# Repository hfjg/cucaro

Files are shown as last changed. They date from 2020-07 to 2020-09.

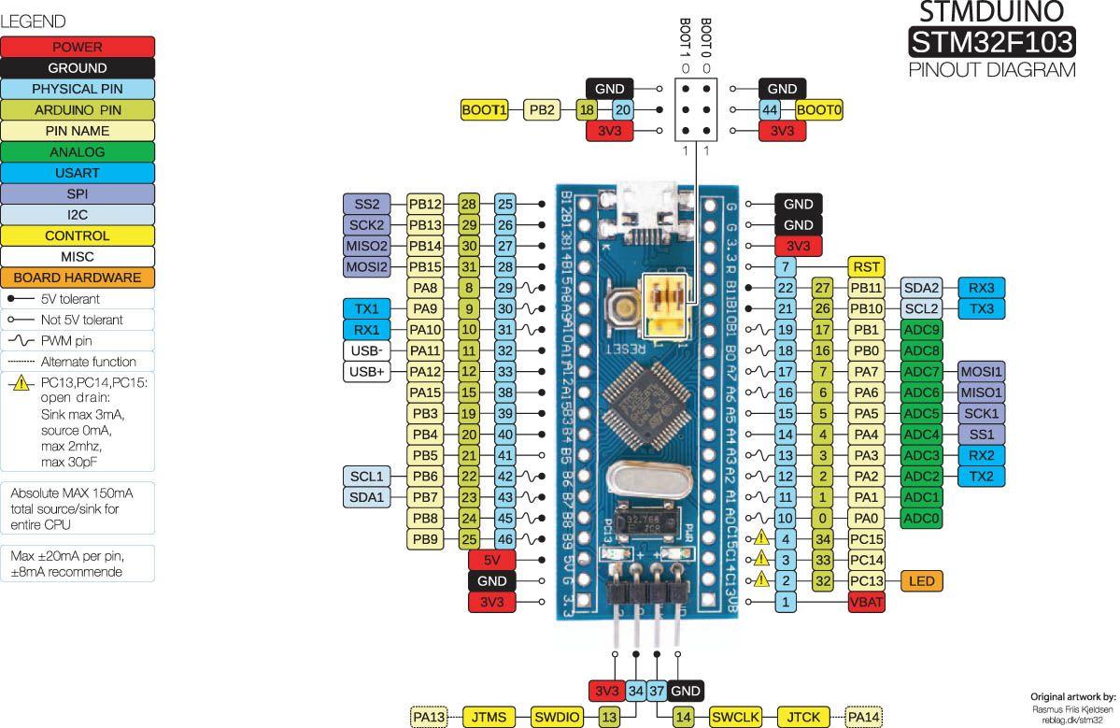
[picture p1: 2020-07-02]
Modules/02_BatMan/Firmware/doc/STM32_Pinout.jpg

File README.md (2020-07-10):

CuCaRo is a **Cu**riosity Inspired **Ca**mera **Ro**ver, roughly adopting the shape, chassis and drive/steer mechanisms.

# Overview
CuCaRo is built of following modules:
(For more details please refer to the module documentation).
1. [Body](./Modules/01_Body/Documents/01_Body_README.md)
2. [BatMan](./Modules/02_BatMan/Documents/02_BatMan_README.md) (The Battery Manager)
3. DriSu (Drive and STeering units, six in total)
3. ACOS (Anti Collision Sensors)
4. RunCam

Modules communicate with each other via CAN-Bus.

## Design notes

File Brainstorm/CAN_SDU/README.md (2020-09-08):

# CAN-SDU
Steer and Drive Unit with CAN-Bus

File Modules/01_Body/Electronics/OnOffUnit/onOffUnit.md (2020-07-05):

#On-Off-Unit
The on-off-unit ensures that the Raspberry Pi is switched off correctly, i.e. it can do ist shutdown process.

## Specification
* One button operation 
    * If off, button press turns on SBC Power Supply
    * If on, short button press initiates reset, long press initiates shutdown

* Additional functions
    * Battery Charge Control
    * Buffered internal battery to initiate shutdown on battery fail during operation
    * Measurement of 
        * Battery voltage
        * Battery Current
        * Charger voltage 
      and option to readout values via I2C.

## Realisation
Microcontroller communicates with SBC via I2C.

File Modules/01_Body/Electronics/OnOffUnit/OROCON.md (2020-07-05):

# OROCON: On-Reset-Off-Controller
OROCON ensures that the Single-Board_Computer (i.e. Raspberry Pi) is shut down correctly.  Communication to SBC is via I2C.

## Specification
* One button operation 
    * If off, button press turns on SBC Power Supply
    * If on, short button press initiates reset, long press initiates shutdown

* Additional functions
    * SLA Battery Charge Control
    * Buffered internal battery to initiate shutdown on battery fail during operation
    * Measurement of 
        * Battery voltage
        * Battery Current
        * Charger voltage 
      and option to readout values via I2C.

## Connectors
* Battery in (XT60)
* Charger in (DC Barrel Jack)

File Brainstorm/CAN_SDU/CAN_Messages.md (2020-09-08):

# Steer Messages
* SetAngleDegrees nn

# Drive Messages

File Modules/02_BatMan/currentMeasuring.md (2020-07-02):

# BatMan Memos

## Current measurement
Sensor will be ACS-712 analog sensor.

Output: U_{ACS}=2500mV + k * I

where 
* k=185mV/A for ACS712-5,
* k=100mV/A for ACS712-20 and 
* k=66mV/A for ACS712-30

For the ADC values this yields:
n_{ADC} = (2^N-1) * U_{ADC}/U_{Ref}

and for the (reverse) sensitivity:
dI/dn = U_{Ref} / (k * (2^N-1) )

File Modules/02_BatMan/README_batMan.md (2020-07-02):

# BatMan
Battery management module for CuCaRo

## Components
* Arduino Pro Mini
* CAN-Interface with MCP2515
* 16-Bit ADC-Module ADS1115
* Current Sensor ACS712
* Temperature Sensor (type tbd)
* 2x LM2596, one for VECU (5V), one for charger

## Firmware functions
- Module attaches as I2C-Slave or as CAN-Module (tbd)
- Periodically measure voltages (10/s),  current (10/s), batteryTemperature (1/s)
- Check for charger, charge if necessary (battery type and data in setup)

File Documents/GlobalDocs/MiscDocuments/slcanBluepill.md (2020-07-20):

#Bluepill as SLCAN adapter

| BluePill | USB-Serial-Adapter | CAN-Transceiver |
|---|---|
| A9 | TX | |
| A10  | RX | |
| A11  | | CRX |
| A12  | TX | CTX |
| 5V | | CAN5V|
| 3V3  | | |
| GND  | GND | GND |

[Firmware here](https://github.com/olliw42/uavcan4hobbyists/blob/master/firmware%20binaries/uc4h-slcan-v009.hex)
Bild:

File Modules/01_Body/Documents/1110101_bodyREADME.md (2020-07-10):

# CuCaRo Body
Since CuCaRo is focused on function (and not on design or appearance of the original), its body is made of a [commercial storage box](https://www.eurobox.de/produktkatalog-eb/stapelbehaelter-geschlossen-400x300x235-mm.html) that holds all the components.

## Components
1. Raspberry Pi as main controller
1. Battery and [BatMan](https://github.com/hfjg/cucaro/blob/master/Modules/02_BatMan/Documents/02_BatMan_README.md)
1. Axis bearings and differential

## Mechanics

## Electronics

## Software
The "main" software on the Raspberry Pi is a collection of [node-red](https://nodered.org/) flows, both for device control and for the user interface.

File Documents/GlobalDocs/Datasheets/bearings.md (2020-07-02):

# Frequently used bearings

[TOC]

## Radial Bearings

### Inner Diameter 6mm
| Name | Inner Diameter/mm | Outer Diameter/mm | Height/mm |
|---|---|---|---|
| MR106 | 6  | 10 | 3 |
| MR126 | 6  | 12 | 4 |
| 686 | 6  | 13 | 5 |
| 626 | 6  | 16 | 6 |

## Axial Bearings
| Name | Inner Diameter/mm | Outer Diameter/mm | Height/mm |
|---|---|---|---|
| F3-8M | 3 | 8,5 | 3,5|
| F6-14M | 6 | 14 | 5|
| F8-16M | 8 | 16 | 5|
| F8-19M | 8 | 19 | 7|
| 51101 | 12 | 26 | 9 |
| 51104 | 20 | 35 | 10 |

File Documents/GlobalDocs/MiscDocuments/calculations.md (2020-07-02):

# Torque Calculations

### Assumptions:
* m = 6 kg
* a = 1 m/s^2
* Wheel diameter 10 cm

### Needed force
F = m a = 6 kg * 1 m/s^2 = 6 N
per wheel
F_w = F/6 = 1 N

### Torque
M = r F = 5 cm * 1 N = 5 Ncm = 50 mN m

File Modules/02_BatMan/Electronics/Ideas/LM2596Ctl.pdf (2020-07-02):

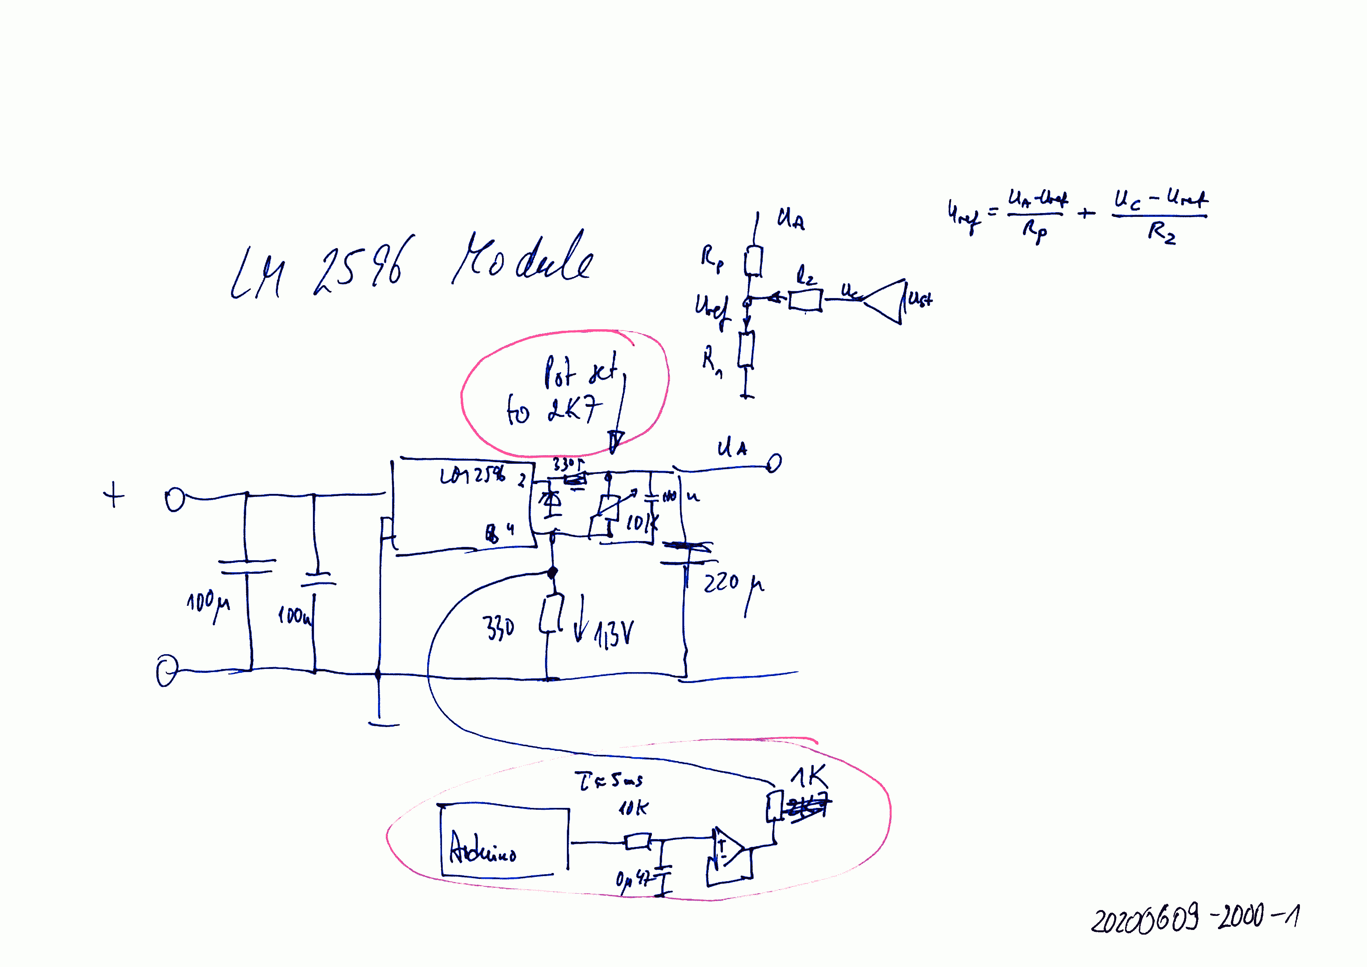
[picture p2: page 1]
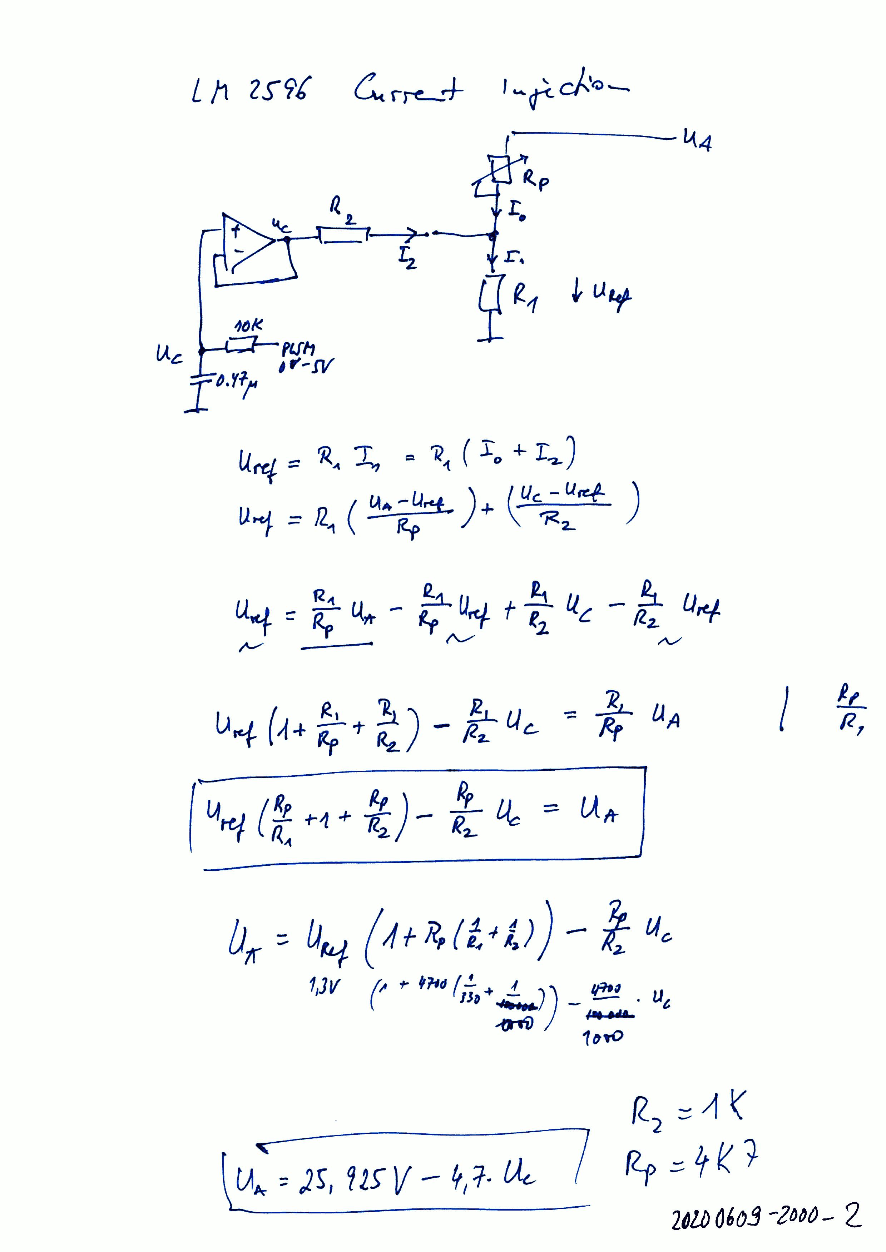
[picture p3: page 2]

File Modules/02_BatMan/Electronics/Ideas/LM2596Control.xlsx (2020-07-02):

U_ref/V | 1.3
R1/Ohm | 330 |  | 1/R1+1/R2
R2/Ohm | 1000 |  | 0.00403030303
 | UC/V
RP/Ohm | 0 | 1 | 2 | 3 | 4 | 5
0 | 1.300 | 1.300 | 1.300 | 1.300 | 1.300 | 1.300
1000 | 6.539 | 5.539 | 4.539 | 3.539 | 2.539 | 1.539
2000 | 11.779 | 9.779 | 7.779 | 5.779 | 3.779 | 1.779
3000 | 17.018 | 14.018 | 11.018 | 8.018 | 5.018 | 2.018
4000 | 22.258 | 18.258 | 14.258 | 10.258 | 6.258 | 2.258
5000 | 27.497 | 22.497 | 17.497 | 12.497 | 7.497 | 2.497
6000 | 32.736 | 26.736 | 20.736 | 14.736 | 8.736 | 2.736
7000 | 37.976 | 30.976 | 23.976 | 16.976 | 9.976 | 2.976
8000 | 43.215 | 35.215 | 27.215 | 19.215 | 11.215 | 3.215
9000 | 48.455 | 39.455 | 30.455 | 21.455 | 12.455 | 3.455
10000 | 53.694 | 43.694 | 33.694 | 23.694 | 13.694 | 3.694
2700 | 15.446 | 12.746 | 10.046 | 7.346 | 4.646 | 1.946
RP/Ohm | 2700
UC/V | UA/V
0 | 15.446
0.2 | 14.906
0.4 | 14.366
0.6 | 13.826
0.8 | 13.286
1 | 12.746
1.2 | 12.206
1.4 | 11.666
1.6 | 11.126
1.8 | 10.586
2 | 10.046
2.2 | 9.506
2.4 | 8.966
2.6 | 8.426
2.8 | 7.886
3 | 7.346
3.2 | 6.806
3.4 | 6.266
3.6 | 5.726
3.8 | 5.186
4 | 4.646
4.2 | 4.106
4.4 | 3.566
4.6 | 3.026
4.8 | 2.486
5 | 1.946

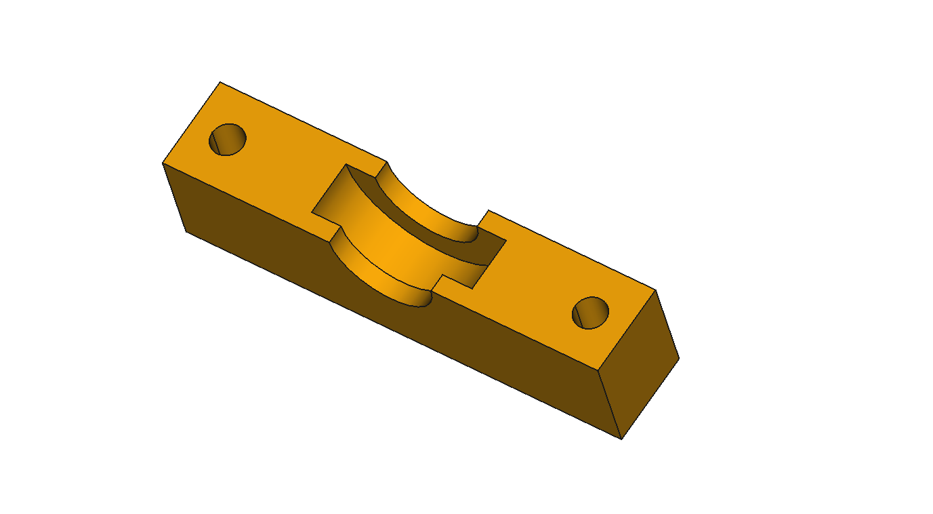
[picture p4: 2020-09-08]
Modules/01_Body/Mechanics/Axis/AxisCarrier/lagerschale_608.png

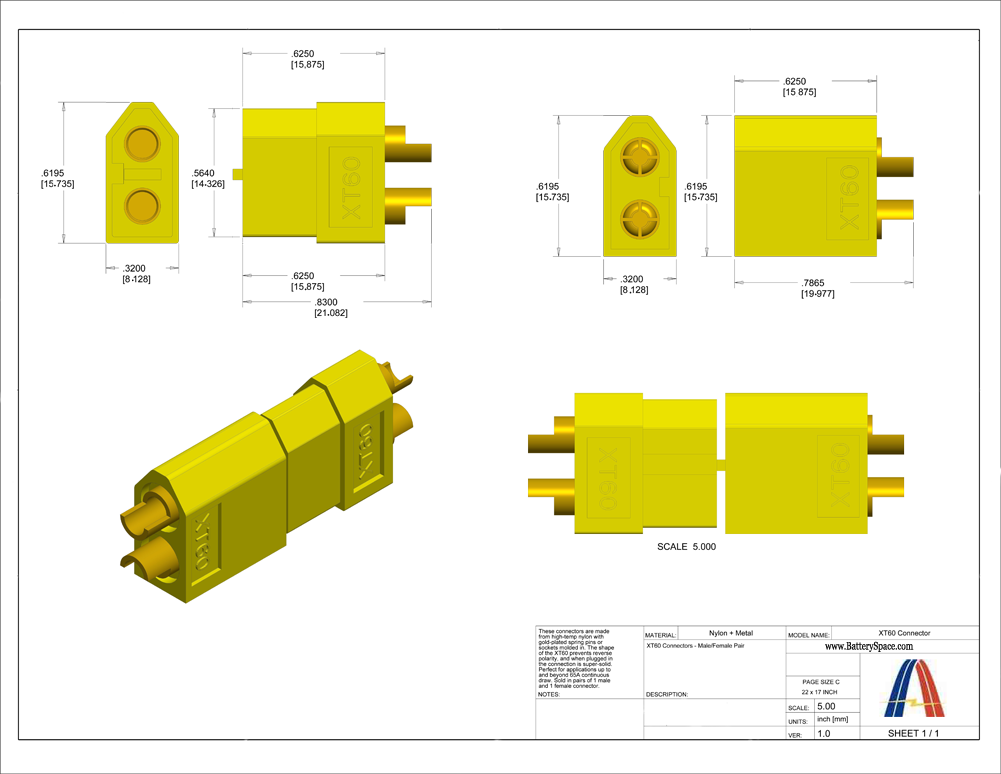
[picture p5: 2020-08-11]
Modules/02_BatMan/Documents/xt60Drawing.png

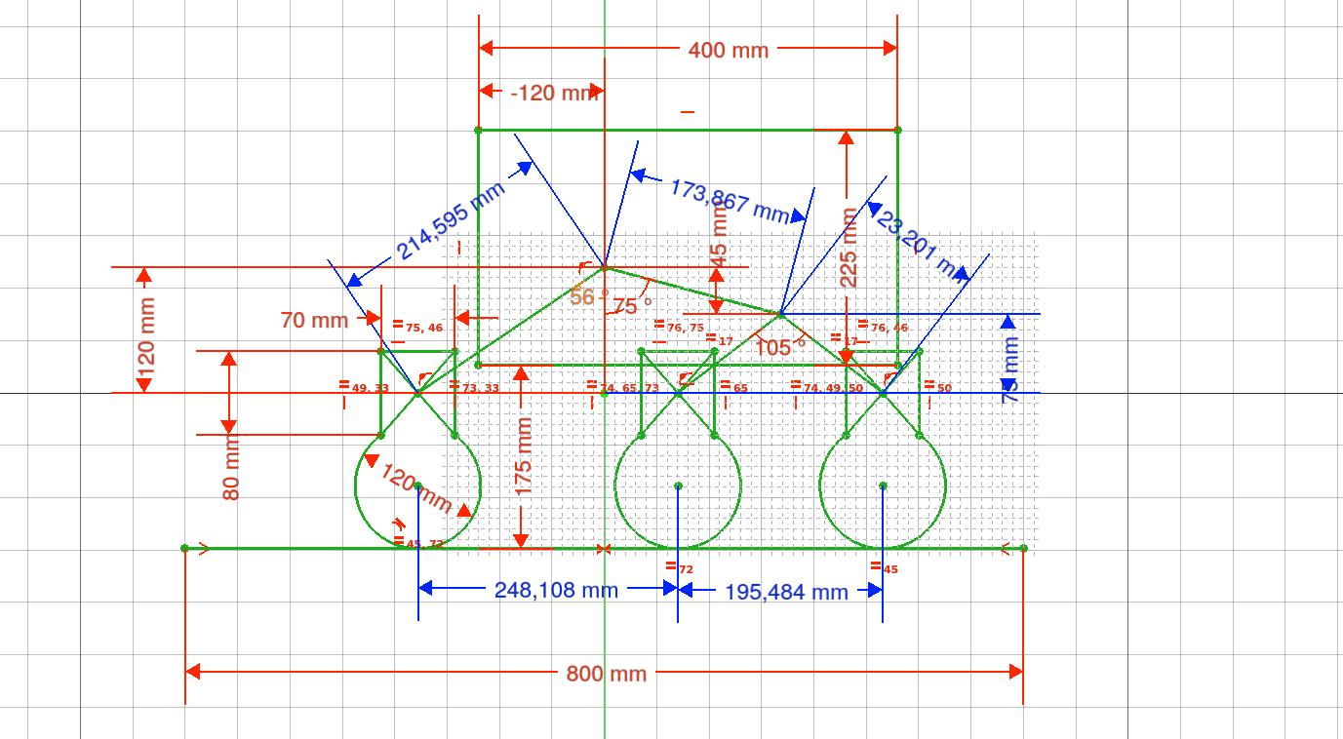
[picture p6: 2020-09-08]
Modules/01_Body/fahrwerk.png

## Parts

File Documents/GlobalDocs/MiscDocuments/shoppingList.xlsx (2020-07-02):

CuCaRo: | Shopping List
Item No. | Desc. | Quantity | Shop | OrderID | exp. Price
1 | TJA1050 | 5 | ebay | 264564374511 | 6.00 €
2 | STM32F103C8T6 | 2 | ebay | 163195692168 | 9.00 €
3 | Servo MG996R | 4+2 | ebay | 254200429981 | 25.00 €
4 | Tires (?) | 4+2 | ebay | 313016459440 | 30.00 €
5 | Pi4-Fan | 1 | berrybase |  | 12.00 €
6 | MPX-Connector | 1x10 | ebay | 221066344116 | 7.95 €
7 | LED-strip | 1 | ebay | 283415013107 | 10.00 €
8 | DC-Dc-Converter, U-I-Limiter | 2 | ebay | 372531513836 | 6.00 €
9 | Dremel Grinder Set |  |  |  | 15.00 €
10
11

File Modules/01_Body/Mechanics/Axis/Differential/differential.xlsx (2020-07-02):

CompNo. | Name | Quantity | Supplier | ItemName
102001 | Body Lower shell | 1 | HG-Printed
102002 | Body Upper shell | 1 | HG-Printed
102003 | Body Fixing Screw | 4 | TBD | M4x20 Allen Head
102004 | Body Fixing Nut | 4 | TBD | M4
102011 | Internal shaft 8 dia x ??? | 1 | TBD
102012 | Internal bevel Gear | 2 | HG-Printed
102013 | Internal Bearing | 2 | GAP | 608
102014 | Internal spacer 8x12x?? | 2 | HG-Printed
102015 | Internal Gear Spacer (optional) | 1 | HG-Printed
102021 | Halfshaft | 2 | TBD | M8x50 Hex Head
102022 | Halfshaft Bearing | 2 | GAP | 608
102023 | Halfshaft spacer 8 x ?? x ?? | 2 | HG-Printed
102024 | Halfshaft bevel Gear | 2 | HG-Printed
102025 | Spacer M8 | 2 | TBD | M8 spacer
102026 | Locknut M8 | 2 | TBD | M8 Locknut

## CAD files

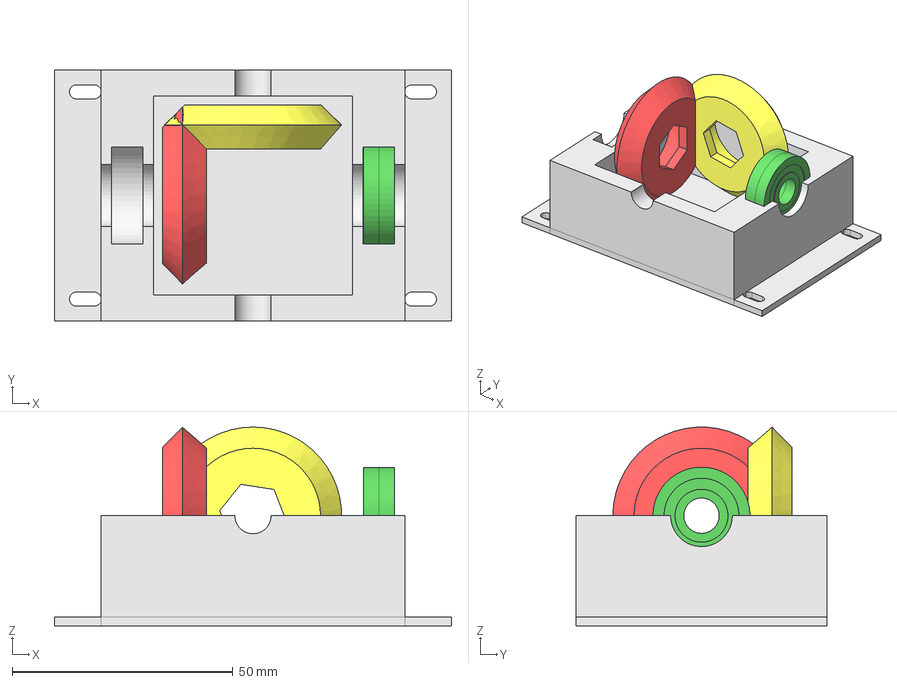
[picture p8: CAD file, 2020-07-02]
Modules/01_Body/Mechanics/Axis/Differential/DiffAssy.FCStd
90.0 x 57.0 x 45.1 mm
cucaroDiff_Box_001
cucaroDiff_608Dummy_001
cucaroDiff_GearwheelDummy_001
cucaroDiff_GearwheelDummy_002

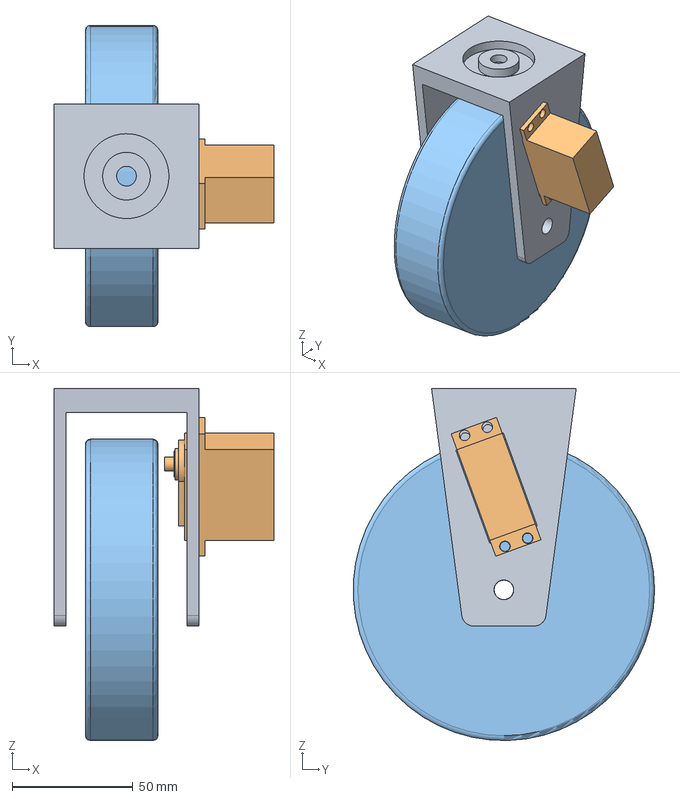
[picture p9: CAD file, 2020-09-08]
Modules/01_Body/Mechanics/Axis/forkHolderAssy.FCStd
91.1 x 124.9 x 146.0 mm
radhalterPollin_001
MG996Dummy_001
radhalterPollin_002

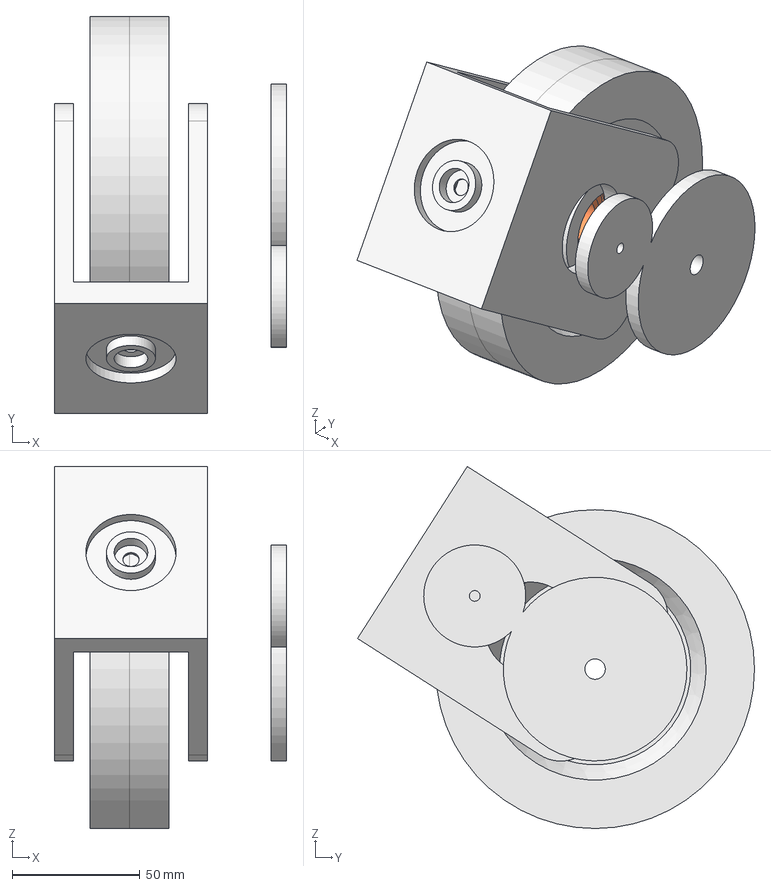
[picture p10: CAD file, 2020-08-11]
Modules/01_Body/Mechanics/Axis/Wheels/pollinWheels/wheelAssy.FCStd
91.0 x 155.7 x 141.9 mm
wheel125_001
bearing6002_001
fork_001
gearWheelDummy_001

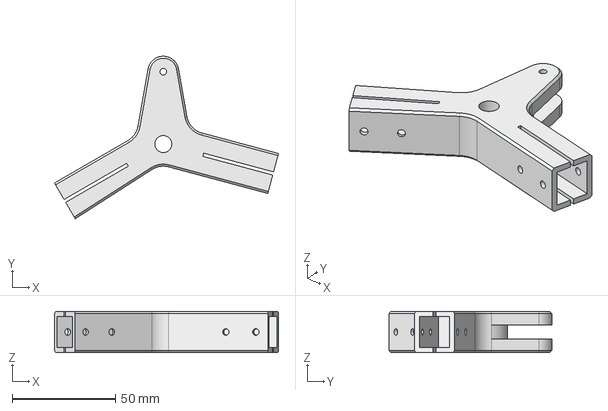
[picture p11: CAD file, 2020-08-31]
axisHolderFront.FCStd
108.3 x 78.7 x 20.0 mm

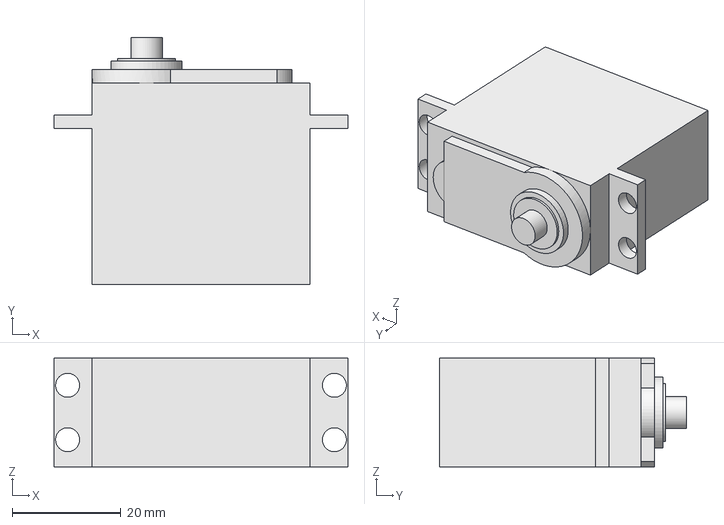
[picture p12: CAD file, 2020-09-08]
Documents/Datasheets/MG996Dummy.FCStd
54.0 x 45.3 x 20.0 mm

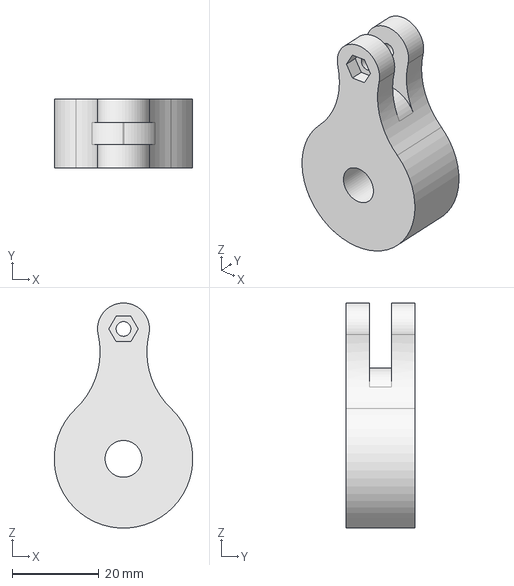
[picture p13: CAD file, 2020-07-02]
Modules/01_Body/Mechanics/Axis/AxisCarrier/EarlierDesigns/schwinge.FCStd
32.0 x 16.0 x 52.0 mm

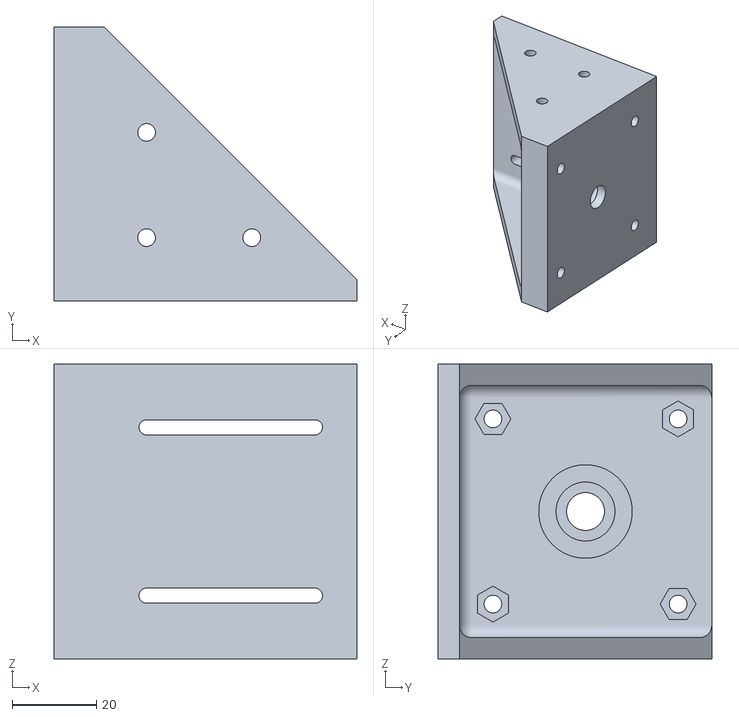
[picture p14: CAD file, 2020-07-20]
Modules/01_Body/Mechanics/Axis/AxisCarrier/STL/axisHolderInner_R03.stl
72.0 x 65.0 x 70.0

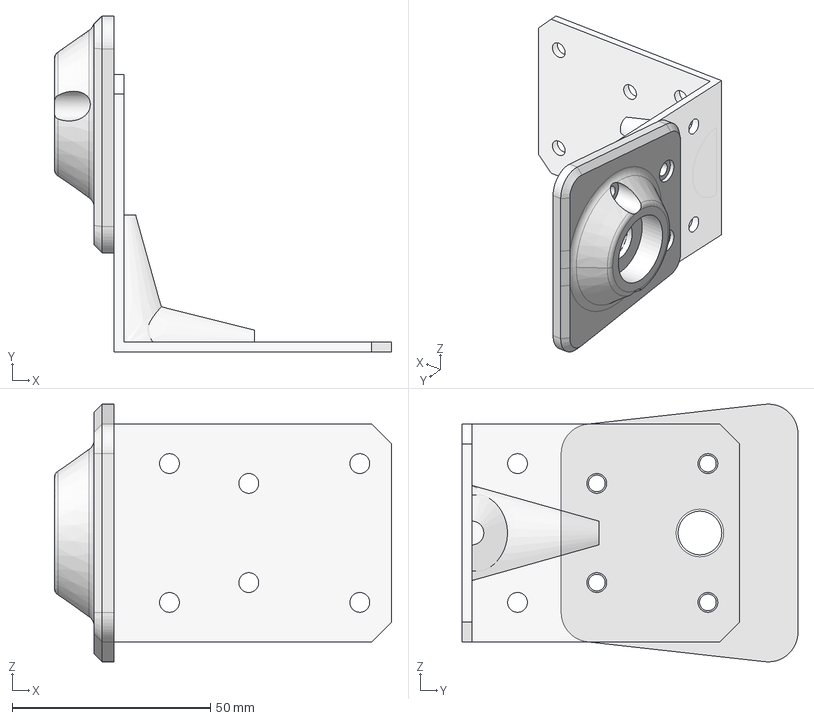
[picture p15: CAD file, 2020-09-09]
Modules/01_Body/Mechanics/Axis/CUAB_CustomAngleBracket.FCStd
85.0 x 84.7 x 65.0 mm
bearingHolderOutside

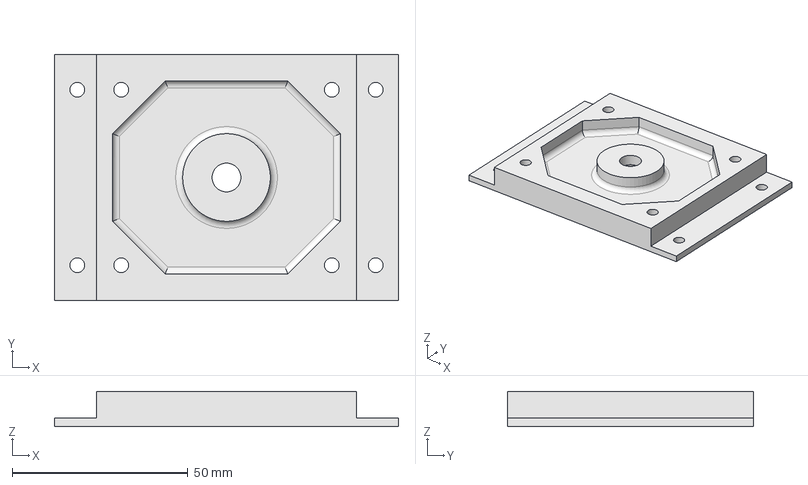
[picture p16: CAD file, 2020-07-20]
Modules/01_Body/Mechanics/Axis/Differential/baseplate.FCStd
98.0 x 70.0 x 10.0 mm

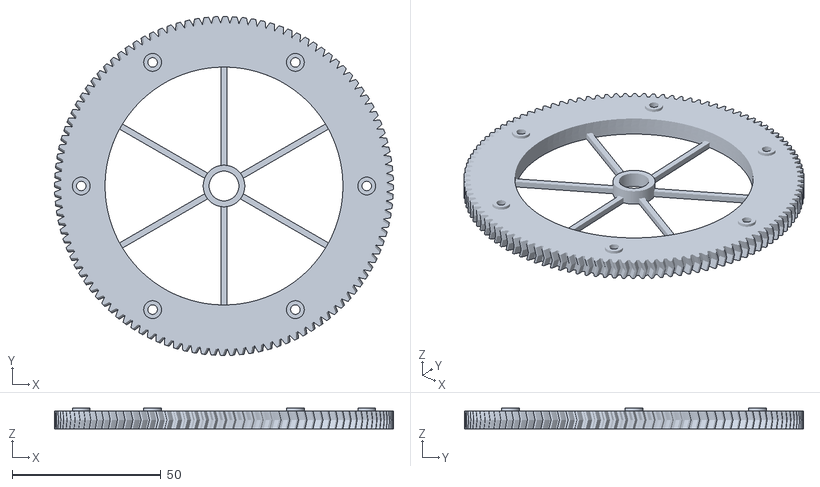
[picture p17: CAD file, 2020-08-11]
Modules/01_Body/Mechanics/Axis/Wheels/pollinWheels/driveGearWheel_02A.stl
114.0 x 114.0 x 6.95

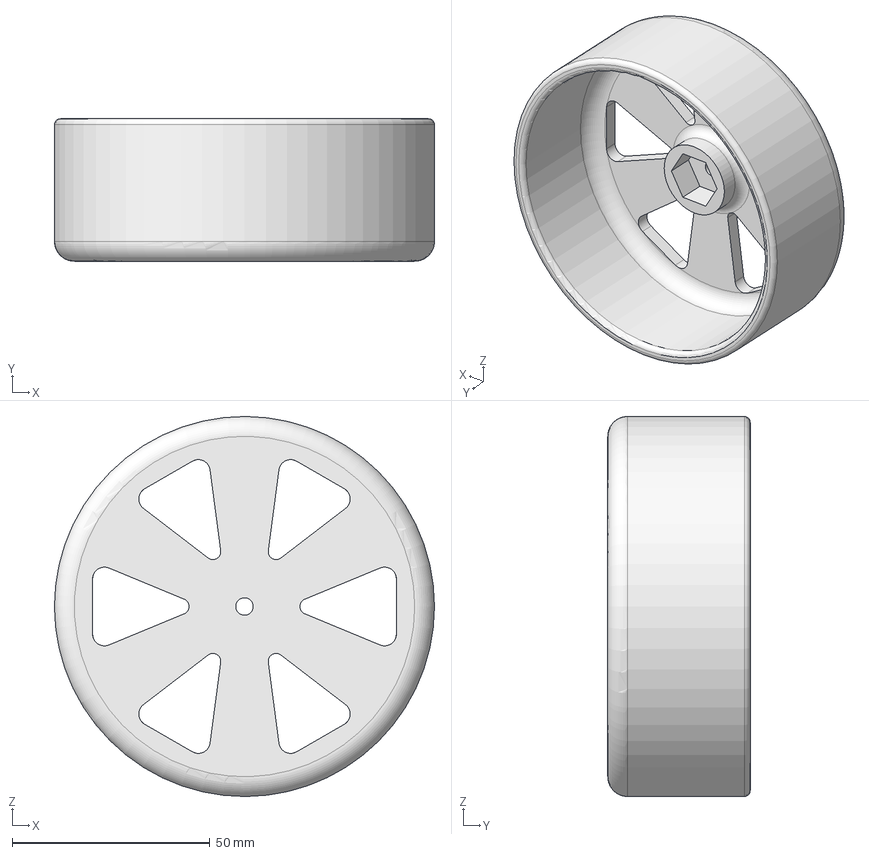
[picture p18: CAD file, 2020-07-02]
Modules/01_Body/Mechanics/Axis/Wheels/wheel_R02.FCStd
96.0 x 36.0 x 96.0 mm

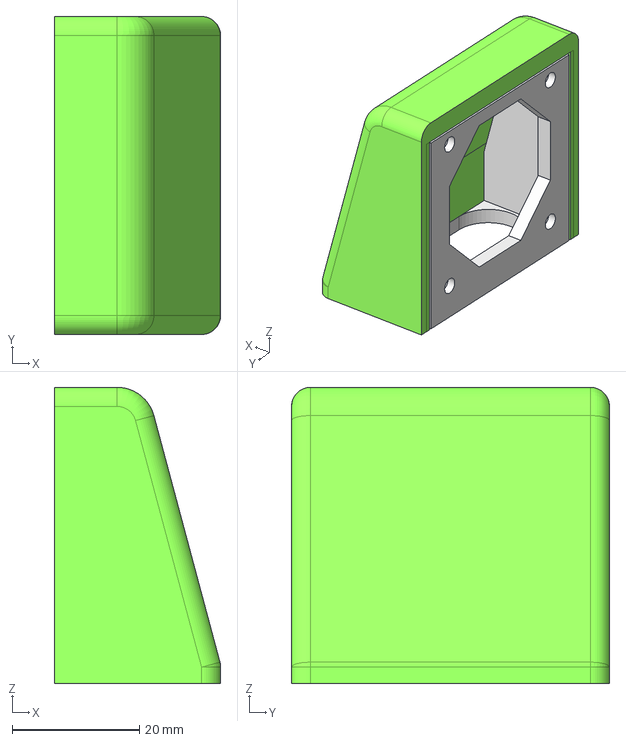
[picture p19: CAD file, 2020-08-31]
Modules/01_Body/Mechanics/Mounts/fanMount_B.FCStd
26.2 x 50.0 x 46.6 mm
wallPlate
cover

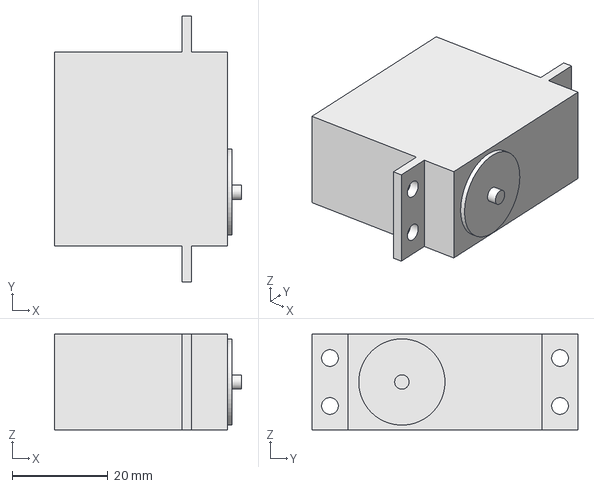
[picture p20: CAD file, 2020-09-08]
Documents/Datasheets/MG995Dummy.FCStd
39.1 x 55.5 x 20.0 mm

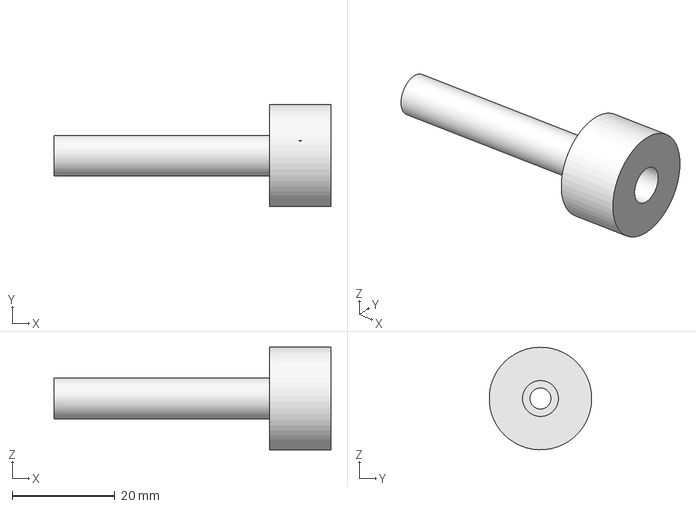
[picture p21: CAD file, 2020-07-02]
Modules/01_Body/Mechanics/Axis/AxisCarrier/EarlierDesigns/radmitnehmerPollin.FCStd
54.0 x 20.0 x 20.0 mm

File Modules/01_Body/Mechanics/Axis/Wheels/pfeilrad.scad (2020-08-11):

use <hg_zahnradlib.scad>
use <baConEl.scad>

zBig = 106;
zSmall = 24;
zModule = 1;
axisDistance = (zBig+zSmall)/2/zModule;
echo("Axis distance = ", axisDistance);

module bigWheel(){
    difference(){
        union(){
            pfeilrad(modul=zModule, zahnzahl=zBig, hoehe=5, bohrung=84, eingriffswinkel = 20, schraegungswinkel = 20);
            tube(do=28.4, wall=2.4, length=6);
            circleOf(num=6, r=28/2, startAngle=30) translate([0,-0.5,0])cube([40,1.4,1.4]);
        }
        
        circleOf(num=6, r=94/2){
            cylinder(d=3.2, h=20, center=true);
            translate([0,0,-0.05])cylinder(d1=5.6, d2=3.2, h=2.2);
           
        }
         circleOf(num=6,r=24)translate([-15,-4,3])cube([8,8,10]);
    }
}

module smallWheel(){
    pfeilrad(modul=zModule, zahnzahl=zSmall, hoehe=4, bohrung=3, eingriffswinkel = 20, schraegungswinkel = -20);
}

bigWheel();

translate([(zBig+zSmall)/2/zModule,0,0.50])rotate([0,0,360/zSmall/2])smallWheel();

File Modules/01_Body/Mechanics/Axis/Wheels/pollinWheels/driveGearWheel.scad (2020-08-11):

use <hg_zahnradlib.scad>
use <baConEl.scad>

module carrier(zz=60, drillDia=8.2, wx=4, pfeil=20){
    difference(){
        union(){
            //pfeilrad(modul=1, zahnzahl=zz, hoehe=6, bohrung=2, eingriffswinkel = 20, schraegungswinkel = pfeil);


  pfeilhohlrad(modul=1, zahnzahl=zz, hoehe=10, randbreite=5, eingriffswinkel = 20, schraegungswinkel = 0);
            
            cylinder(d=40, h=2);
            for (phi=[0:90:179]) rotate([0,0,phi])translate([-(zz-5)/2,-wx/2,-3])
                cube([zz-5,wx,3]);
        }
        cylinder(d=drillDia, h=20, center=true);
    }
}

r = 45;
zh = 6;
z1 = 12;
z2 = z1 + 2*r;

color("green")translate([r,0,0])pfeilrad(modul=1, zahnzahl=z1, hoehe=zh, bohrung=4, eingriffswinkel = 20, schraegungswinkel = -15);

!union(){
    difference(){
        translate([0,0,-2]){
            translate([0,0,-3])tube(di=80, do=114.333, length=3);
            tube(di=105, do=114.333, length=3);
            translate([0,0,-3])tube(di=8.2, do=14, length=3);
            
            circleOf(r=6, num=6, startAngle=30)translate([0,-4,-3])cube([45,8,3]);
        }
        circleOf(r=45, num=6){
           cylinder(d=3.2, h=20, center=true);
           translate([0,0,-3+0.05])cylinder(d2=5.8, d1=3.2);
        }
    }

    pfeilhohlrad(modul=1, zahnzahl=z2, hoehe=zh, randbreite=5, eingriffswinkel = 20, schraegungswinkel = 15);
}

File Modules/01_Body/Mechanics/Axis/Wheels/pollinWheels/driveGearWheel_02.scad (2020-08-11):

use <hg_zahnradlib.scad>
use <baConEl.scad>

zh = 6;
z1 = 48;
z2 = 112;
r = (z1+z2)/2;
screwDia = 3.2;

echo ("r = ", r);
echo ("gear ratio = ", z2/z1);

module antrieb(){
    color("green")translate([r,0,0])pfeilrad(modul=1, zahnzahl=z1, hoehe=zh, bohrung=4.2, eingriffswinkel = 20, schraegungswinkel = -15);
}


module abtrieb(){
   
    difference(){
        union(){
            pfeilrad(modul=1, zahnzahl=z2, hoehe=zh, 
            bohrung=z2-32, eingriffswinkel = 20,
            schraegungswinkel = 15);
        
        // hub
            tube(di=10, wall=2, length=5);
        
        // spokes (break away after monting gearwheel)
            spokeWidth = 2;
            spokeHeight = 2;
            circleOf(r=6, num=6, startAngle=30)
                translate([0,-spokeWidth/2,0])cube([z2/2-10,spokeWidth,spokeHeight]);
            circleOf(r=z2/2-8, num=6)
               translate([0,0,zh-0.05])tube(di=screwDia, do=6, length=1);
        }
        
        // mount holes
        circleOf(r=z2/2-8, num=6){
           cylinder(d=screwDia, h=20, center=true);
           translate([0,0,-0.05])cylinder(d1=5.8, d2=screwDia);
        }
    }

}

wheelWidth = 32;
translate([0,0,-(wheelWidth/2+1+zh)]){
    antrieb();
    !abtrieb();
}
%axis();
%wheel();

module axis(){cylinder(d=8, h=60, center=true);}
module wheel(){tube(do=120, di=8, length=32, center=true);}

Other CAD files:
Modules/01_Body/skizzeFahrwerk.FCStd
Modules/01_Body/Mechanics/Axis/AxisCarrier/STL/flexibleCoupling-8x8x30.stl
Modules/01_Body/Mechanics/Axis/Wheels/pollinWheels/wheel125.FCStd
Modules/01_Body/Mechanics/Mounts/fanMount_A1.FCStd
Modules/01_Body/Mechanics/Axis/AxisCarrier/Flexible_Coupling.scad
Modules/01_Body/Mechanics/Axis/1220403_axisHolderFrontBase.FCStd
Modules/01_Body/Mechanics/Axis/1220403_axisHolderFrontLeftInner.FCStd
Modules/01_Body/Mechanics/Axis/1220403_axisHolderFrontLeftOuter.FCStd
Modules/01_Body/Mechanics/Axis/1220403_axisHolderLeftInner.stl
Modules/01_Body/Mechanics/Axis/1220403_axisHolderLeftOuter.stl
Modules/01_Body/Mechanics/Axis/AxisCarrier/1110101_axisAssy.FCStd
Modules/01_Body/Mechanics/Axis/AxisCarrier/1210101_axisCarrierPlate.FCStd
Modules/01_Body/Mechanics/Axis/AxisCarrier/1220105_axisHolderOuter.FCStd
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

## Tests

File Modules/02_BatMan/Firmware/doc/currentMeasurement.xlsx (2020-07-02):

ACS712 calculations |  |  | V_REF/mV | N | V_REF/mV | N
 |  |  | 5000 | 10 | 3300 | 12
Model | Sensitivity / (mV/A) | Offset / mV | mA per LSB |  | mA per LSB
ACS712-5 | 185 | 2500 | 26.4 |  | 6.6
ACS712-20 | 100 | 2500 | 48.9 |  | 12.2
ACS712-30 | 66 | 2500 | 74.1 |  | 18.5

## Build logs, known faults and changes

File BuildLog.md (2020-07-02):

# Build Log

## 2020-05-01
Finished wheel assembly, printed test parts (hex hub and lower axial bearing holder).

## 2020-04-13
Ported Differential ends to OpenSCAD. To omit heat inserts, redesigned ends as cylinder and hat. Cylinder holds M8 nut for the differential bar, hat holds M3 nut for turnbuckle. The two parts are screwed together with 3 M3 screws.
Printing: Hat should be printed small end down, usung brim if necessary. Cylinder shoulf be printed with M8-nut up. Both parts with no supports!

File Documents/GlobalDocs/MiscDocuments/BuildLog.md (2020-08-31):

# Build Log

## 2020-08-13
Printed front axle joint. Failed due to tangled filament. 
**Idea:** Print in two halves -> needs no supports, easier in case of printing failure.

## 2020-07-05
Added holes to differential's halfshaft bevel gear.

## 2020-05-01
Finished wheel assembly, printed test parts (hex hub and lower axial bearing holder).

## 2020-04-13
Ported Differential ends to OpenSCAD. To omit heat inserts, redesigned ends as cylinder and hat. Cylinder holds M8 nut for the differential bar, hat holds M3 nut for turnbuckle. The two parts are screwed together with 3 M3 screws.
Printing: Hat should be printed small end down, usung brim if necessary. Cylinder shoulf be printed with M8-nut up. Both parts with no supports!

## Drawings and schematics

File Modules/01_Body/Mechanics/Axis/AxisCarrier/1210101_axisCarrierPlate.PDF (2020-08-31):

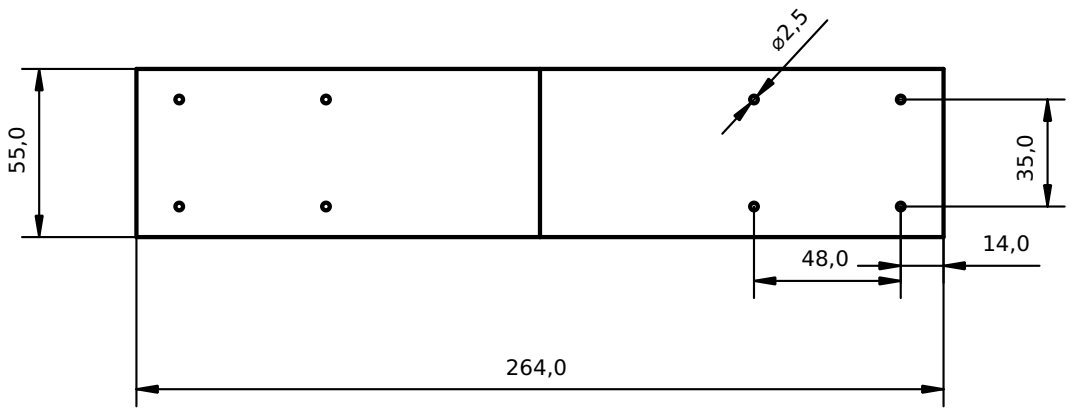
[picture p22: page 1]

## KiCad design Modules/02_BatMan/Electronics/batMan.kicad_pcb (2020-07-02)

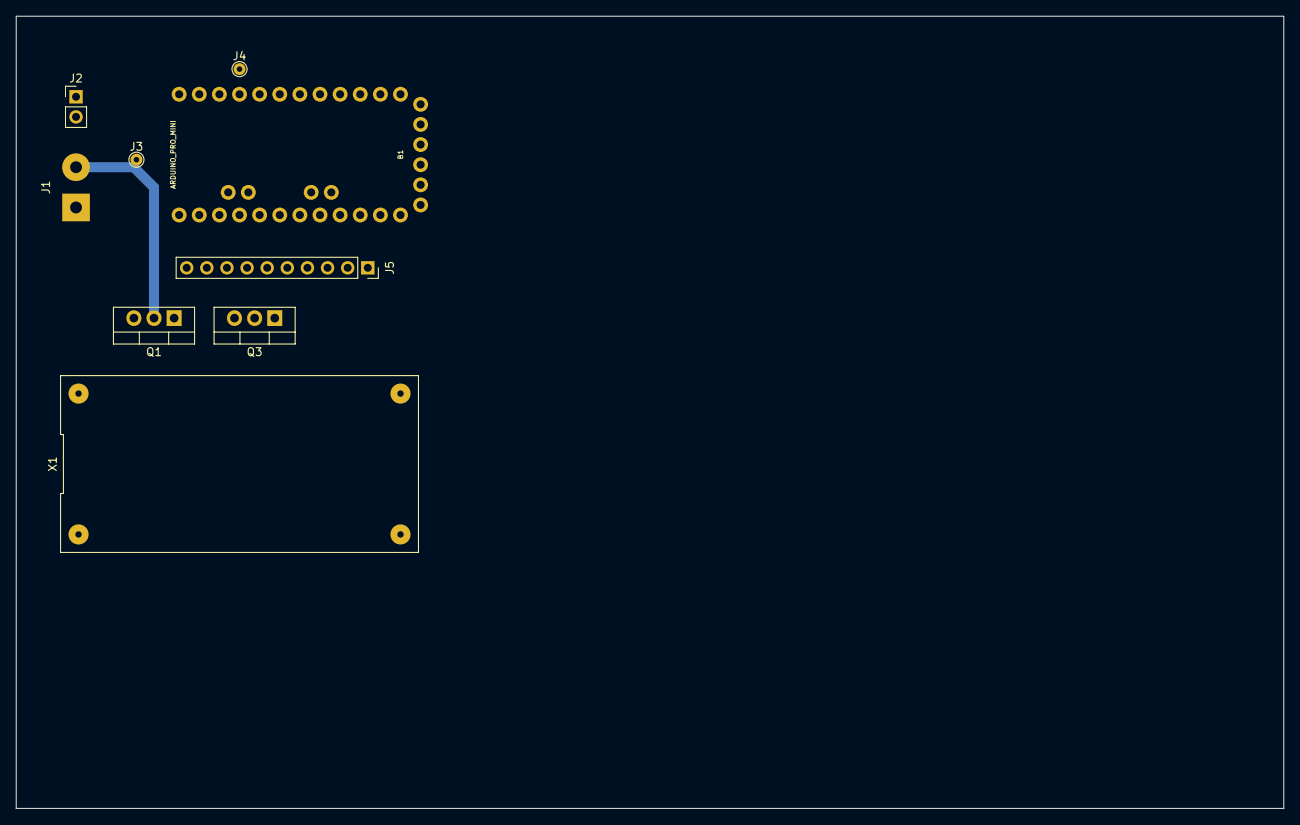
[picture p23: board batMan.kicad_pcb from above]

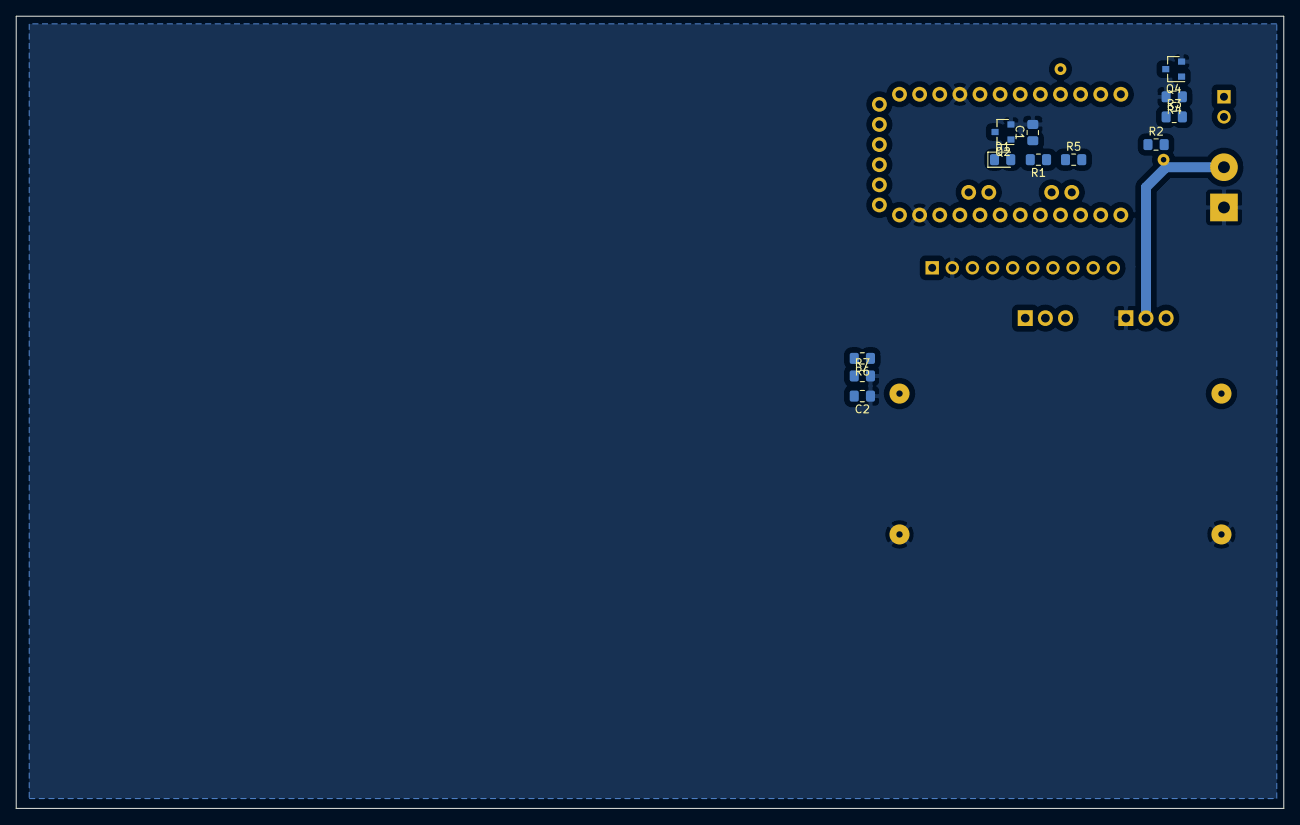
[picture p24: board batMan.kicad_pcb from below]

Board: 2 copper layers, 160.0 x 100.0 mm, 21 parts (12 on the bottom side), 16 nets.

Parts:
B1: ARDUINO_PRO_MINI
C1, C2: 100n; C_0805_2012Metric_Pad1.15x1.40mm_HandSolder
D1: LED; LED_0805_2012Metric_Pad1.15x1.40mm_HandSolder
J1: PWR_IN; SolderWirePad_1x02_P5.08mm_Drill1.5mm
J2: BUT,TON; PinHeader_1x02_P2.54mm_Vertical
J3: TP2; TestPoint_THTPad_D1.5mm_Drill0.7mm
J4: TP1; TestPoint_THTPad_D1.5mm_Drill0.7mm
J5: ADS1115; PinSocket_1x10_P2.54mm_Vertical
Q1, Q3: IRF5305; TO-220-3_Vertical
Q2, Q4: BC847; SOT-23
R1, R3, R4, R5, R6, R7: 10K; R_0805_2012Metric_Pad1.15x1.40mm_HandSolder
R2: 1K; R_0805_2012Metric_Pad1.15x1.40mm_HandSolder
X1: DCDC_Buck_Module3A; DIP-4_700

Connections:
/A0: C2.2, J5.7, R6.2, R7.1
/BAT+: J1.2, Q1.2
/BUTTON: B1.9, J4.1, Q4.3
/PWR_HOLD: B1.10, J3.1, R5.2
/SCL: B1.A5, J5.3
/SDA: B1.A4, J5.4
/VBAT: Q1.3, Q3.3, R2.1
/VBAT_SW: Q3.2, R6.1, X1.4
GNDPWR: B1.4, B1.23, C1.2, C2.1, J1.1, J5.2, Q1.1, Q2.2, Q4.2, R4.2, R7.2, X1.1, X1.2
unnamed: C1.1, R1.1, R5.1
unnamed: D1.1, Q2.3
unnamed: D1.2, J2.2, R3.2
unnamed: J2.1, Q4.1, R4.1
unnamed: Q2.1, R1.2
unnamed: Q3.1, R2.2, R3.1
VCC: B1.21, J5.1, X1.3

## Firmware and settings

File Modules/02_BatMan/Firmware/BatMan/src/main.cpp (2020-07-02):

<<<<<<< HEAD
#include <Arduino.h>

#include <Adafruit_ADS1015.h>
Adafruit_ADS1015 adc;

#include <SPI.h>
#include "mcp_can.h"


#include "chargeController.h"

enum {E_NO_ERROR, E_CAN_INIT_ERROR, E_WRONG_PARAMETER};
enum {ADC_VBAT_CHANNEL, ADC_VCHG_CHANNEL, ADC_IBAT_CHANNEL, ADC_TBAT_CHANNEL};
enum {POLARITY_TRUE, POLARITY_INVERTED};

#define spiCSPin 10
MCP_CAN CAN(spiCSPin);
#define MAX_PDO_PERIOD 10000

#define CHARGE_ENABLE_PIN 4
#define CHARGE_ENABLE_INVERTED 0

// Cave! Pro Mini PWM only on 3, 5, 6, 9, 10, 11
#define CHARGE_PWM_PIN 5
#define CHARGE_PWM_INVERTED 1

#define PIN_BUTTON 6

#define PIN_POWER_HOLD 7
#define POLARITY_PIN_POWER_HOLD 1

#define NODE_ID 0x11
#define LOOP_TIME 500

struct {
  union{
    struct {
      char chargerPresent : 1;
    }flag;
    uint8_t statusByte;
  } status;
  int8_t tBatteryCelsius;
  uint16_t vBatteryMillivolt;
  uint16_t iBatteryMilliamp;
  uint16_t vChargerMillivolt;
}processData;


struct{
    uint16_t vBatteryMax;
    uint16_t vBatteryMin;
    uint16_t vBatteryChargeBegin;
    uint16_t iChargeMax;
}sdo;

typedef struct{
  uint8_t rp, rn;
} s_adcCfg;

struct{
  s_adcCfg adcChannelConfig[4]={{1,1},{2,2},{3,3}, {4,4}};
}serviceData;

boolean dataChange;



uint8_t initCAN(uint8_t canBaud){
  if (CAN.begin(CAN_500KBPS) != CAN_OK)
    return E_CAN_INIT_ERROR;
  else
    return E_NO_ERROR;
}

void initADC(adsGain_t  gain){
  adc.begin();
  adc.setGain(gain); // 1x gain   +/- 4.069V  1 bit = 0.125mV
}

uint8_t getADCmillivolts(uint16_t *result, uint8_t channel){
  if (channel > 3)
    return E_WRONG_PARAMETER;
  else {
    *result = adc.readADC_SingleEnded(channel)/adc.getGain()/8;
    return E_NO_ERROR;
  }
}

uint16_t getBatteryVoltage(void){
  return adc.readADC_SingleEnded(0)/adc.getGain()/8;
}

uint16_t getChargerVoltage(void){
  return adc.readADC_SingleEnded(1)/adc.getGain()/8;
}

 chargeController* initCharger(){
  chargeController *A;
  A = new chargeController(
        CHARGE_PWM_PIN,
        CHARGE_PWM_INVERTED,
        CHARGE_ENABLE_PIN,
        CHARGE_ENABLE_INVERTED
      );
      return A;
}

void setup(){
  digitalWrite(PIN_POWER_HOLD, 1^POLARITY_PIN_POWER_HOLD);
  pinMode(PIN_POWER_HOLD, OUTPUT);

  pinMode(PIN_BUTTON, INPUT_PULLUP);

  // init charger
  chargeController* CC = initCharger();
  // set callback functions
  CC->setBatteryVoltageCB(getBatteryVoltage);
  CC->setChargerVoltageCB(getChargerVoltage);
  // set limits
  CC->setVoltageDead(9700);
  CC->setVoltageBeginCharge(12000);
  CC->setVoltageTerminateCharge(13800);
  CC->setChargeCurrentMax(700);
  CC->setTemperatureMax(50);


  Serial.begin(115200);
  initCAN(CAN_500KBPS);
  initADC(GAIN_ONE);
}

uint8_t adcRead(void){
  s_adcCfg *p;
  uint16_t scratchpad;

  uint8_t returnValue = 0;

  for (uint8_t channel=0; channel<4; channel++){
    getADCmillivolts(&(scratchpad), channel);
    p = &(serviceData.adcChannelConfig[channel]);
    switch(channel){
      case ADC_VBAT_CHANNEL:
        scratchpad *= (p->rp+p->rn)/p->rn;
        if (scratchpad != processData.vBatteryMillivolt){
          ++returnValue;
          processData.vBatteryMillivolt = scratchpad;
        }
        break;
      case ADC_VCHG_CHANNEL:
        scratchpad *= (p->rp+p->rn)/p->rn;
        if (scratchpad != processData.vChargerMillivolt){
          ++returnValue;
          processData.vChargerMillivolt = scratchpad;
        }
        break;
      case ADC_IBAT_CHANNEL:
        scratchpad *= 1000/100; // mA/mV
        if (scratchpad != processData.iBatteryMilliamp){
          ++returnValue;
          processData.iBatteryMilliamp = scratchpad;
        }
        break;
      case ADC_TBAT_CHANNEL:
        processData.tBatteryCelsius = scratchpad; // TBD
        break;
      default:
        break;
    }
  }
  return returnValue;
}


void doWork(void){

  // get ADC values
  if (adcRead())
    dataChange = 1;

  //chargeControl();



}


void loop(){
  uint32_t lastRun;
  static uint32_t lastTransmission= millis();

  lastRun = millis();

  doWork();

  // send PDO
  // if dataChanged or max PDO time elapsed
  if(dataChange || (millis()-lastTransmission >= MAX_PDO_PERIOD)) {
    dataChange = false;
    lastTransmission = millis();
    CAN.sendMsgBuf(
      0x180+NODE_ID,
      0,
      sizeof(processData),
      (byte*)(&processData)
    );
  }

  while( (millis()-lastRun) < LOOP_TIME)
    ;
=======
/**
 \mainpage

 # BatMan
 BatMan ist the Battery Manager Module for CuCaRo. It is closely coupled to
 the Central Electronics Module (Raspberry Pi 4) via TWI-Bus.

 ## Hardware
 The BatMan hardware consists of
 ### Microcontroller
    <a href="https://www.arduino.cc/en/pmwiki.php?n=Main/ArduinoBoardProMini">
    Arduino Pro Mini</a> (5V, 16MHz)
 ### Level Shifter
    Level shifter module for the connection with the RaspberryPi4 I2C
 ### Current sensor module
    <a href="https://www.allegromicro.com/~/media/files/datasheets/acs712-datasheet.ashx">ACS712-20</a> (+/-20A, sensitivity 100mV/A, offset
    voltage ist 2500mV)
 ### Analog-Digital-Converter
    16-Bit-Analog-digital-converter module
    <a href="http://www.ti.com/lit/ds/symlink/ads1115.pdf">
    ADS1115</a> with integrated precision reference.
    This is necessary to achieve sufficient resolution and precision
    of voltage measurement when using Lithium-based batteries and also for
    sufficient precision of the current measurement wit th
    ACS712-20 module.
  ### DC-DC-Converters
  - a fixed-output DC-DC-Buck-Converter V_Bat -> 5V @ 10A for servos
  - a fixed-output DC-DC-Buck-Converter V_Bat -> 5V @ 3A for the CEM
  - a variable-output DC-DC-Converter for V_Charge -> V_Bat

  ### Power on/off/reset button
    One button for on/off if pressed for a short time, reboot if pressed for a
      long time


  ## Software
  The software takes care of following tasks:
  - Take periodic samples of battery and charger voltages, current and
    temperature and update I2C registers accordingly, force shutdown after
    communication timeout of battery breakdown.
  - Control charging (if charger attached)
  - Receive and execute commands in I2C command register
  - Check button and execute command accordingly

Configuration is read from and written to EEPROM. If EEPROM routines find a
checksum error, EEPROM and I2C registers are set to defaults.

  \todo Implement small battery for controlled shutdown if battery was
      removed accidentally.
**/

#include <Arduino.h>
#include <EEPROM.h>

#include "hardware.h"
#include "ctwi.h"
#include "adc.h"
#include "keys.h"
#include "charge.h"
#include "battery.h"
#include "helpers.h"
#include "errors.h"

#define DEBUG


#ifdef DEBUG
#define dprint(x) Serial.print(x)
#else
#define dprint(x) ;
#endif

s_i2cReadRegs i2cReadRegs;
s_i2cControlRegs i2cControlRegs;


/**
 \brief Call all initialization routines
**/
void setup() {

  hardwareInit();
  ctwiInit(&i2cReadRegs, &i2cControlRegs);
  adcInit(1);

#ifdef DEBUG
  Serial.begin(115200);

  Serial.println(i2cControlRegs.voltageMin);
  Serial.println(i2cControlRegs.voltageChargeBegin);
  Serial.println(i2cControlRegs.voltageMax);
  Serial.println(i2cControlRegs.tMin);
  Serial.println(i2cControlRegs.tMax);
  Serial.println(i2cControlRegs.vChargerMin);
  Serial.println(i2cControlRegs.vChargerMax);
  Serial.println(i2cControlRegs.iBatteryCharge);
#endif
}


/**
 \brief Save state to EEPROM, then shutdown
**/
void shutdown(void){
  EEPROM.put(0, i2cControlRegs);
  EEPROM.put(sizeof(s_i2cControlRegs),
      checksum((uint8_t *)(&i2cControlRegs), sizeof(s_i2cControlRegs)) );

  // switch off myself
  digitalWrite(PIN_POWER_HOLD, 0);
}

/**
* \brief Main loop
**/
void loop() {
uint32_t lastSample, shutdownTriggerTime;

  lastSample = millis();

  //sampleADC();
  getVoltageMillivolts(&(i2cReadRegs.vCharger), ADS_V_CHARGER, 68, 10);
  getVoltageMillivolts(&(i2cReadRegs.vBattery), ADS_V_BATTERY, 33, 10);
  getCurrentACS712(&(i2cReadRegs.iBattery), ADS_I_BATTERY, 20);
  getVoltageMillivolts((uint16_t*)(&(i2cReadRegs.tBattery)), ADS_T_BATTERY, 1, 1);

  dprint("\nUpdated i2cReadRegs");

  // set status bits
  i2cReadRegs.state.flag.batteryLow =
    (i2cReadRegs.vBattery <= i2cControlRegs.voltageChargeBegin);

  // i2cRegs are updated in background, check for twi commands
  if (i2cControlRegs.command.shutdown){
    i2cReadRegs.state.flag.shutdownAck = 1;
    i2cControlRegs.command.shutdown = 0; //reset command
    shutdownTriggerTime = lastSample;
  }


  // control charger
  int16_t ichg = charge(&i2cReadRegs, &i2cControlRegs);
  dprint("\nCharge PWM : "); dprint(ichg);

  switch(checkKey(PIN_BUTTON)){
    case KEY_SHORT:
      i2cReadRegs.state.flag.shutdownRequest = 1;
      i2cReadRegs.state.flag.rebootRequest = 0;
      break;
    case KEY_LONG:
      i2cReadRegs.state.flag.shutdownRequest = 0;
      i2cReadRegs.state.flag.rebootRequest = 1;
      break;
    default:
      i2cReadRegs.state.flag.shutdownRequest = 0;
      i2cReadRegs.state.flag.rebootRequest = 0;
      break;
  }

  if ( (millis() - shutdownTriggerTime) >= i2cControlRegs.shutdownTimeMillis)
    shutdown();

  // idle for rest of sampling time
  while ( (millis()-lastSample) < i2cControlRegs.sampleTimeMillis)
    ;



>>>>>>> 7a67c6e417c95918f84fa9c0a225ee67cc05a434
}

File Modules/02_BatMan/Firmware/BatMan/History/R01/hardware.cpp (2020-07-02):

/****************************
* hardware initialization
******************************/
#include <Arduino.h>
#include "hardware.h"


void hardwareInit(void){
  pinMode(PIN_BUTTON, INPUT_PULLUP);

  pinMode(PIN_POWER_HOLD, OUTPUT);
  digitalWrite(PIN_POWER_HOLD, 1);

  pinMode(PWR_SWITCH_CHARGER, OUTPUT);

  digitalWrite(CHARGER_PWM, 1);
  pinMode(CHARGER_PWM, OUTPUT);
}

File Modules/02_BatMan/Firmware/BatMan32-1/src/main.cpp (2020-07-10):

#include <Arduino.h>
#include <eXoCAN.h>
eXoCAN can;
#define CANOPEN_NODE_ID 2

#define PIN_vBattery 10
#define PIN_iBattery 11
#define PIN_vCharger 12
#define PIN_CHARGER_ENABLE 6

#define TXPDO0_ID 0x180+CANOPEN_NODE_ID
#define RXPDO0_ID 0x200+CANOPEN_NODE_ID
#define EMCY_ID   0x080+CANOPEN_NODE_ID
#define RXSDO_ID  0x600+CANOPEN_NODE_ID
#define bluePillLED PC13

#define MEASURE_LOOP_TIME 1000
#define digitalToggle(x)  digitalWrite(x, !digitalRead(x))

enum e_keyPress {NONE, SHORT, LONG, UNDEF};
enum e_emergencies {EMCY_BATTERY_DEAD, EMCY_CHARGER_OVERVOLTAGE, EMCY_CHARGER_FAIL};

typedef struct{
    struct{
      uint8_t chargerConnected : 1;
      uint8_t charging : 1;
      e_keyPress keypress : 2;
    }
    flag;
    uint16_t vBatteryMillivolts;
    int16_t iBatteryMilliamps;
    uint16_t vChargerMillivolts;
}s_TXPDO;
s_TXPDO txpdo;

uint8_t CANrxBytes[8];

struct{
  uint16_t vBatteryMin, vBatteryMax, vBatteryStartCharge;
  uint16_t vChargerMin, vChargerMax;

}sdo;

void emergency (uint8_t emcyNumber){

  // can.transmit(txMsgID, txData, txDataLen);
  can.transmit(EMCY_ID, &emcyNumber, sizeof(uint8_t));
}

void canISR() // get CAN bus frame passed by a filter into fifo0
{ int id=RXPDO0_ID;
  int fltIdx=0;

  can.receive(id, fltIdx, CANrxBytes);  // empties fifo0 so that another another rx interrupt can take place
}

void setup() {
  // put your setup code here, to run once:
  digitalWrite(PIN_CHARGER_ENABLE, LOW);
  pinMode(PIN_CHARGER_ENABLE, OUTPUT);

  can.begin(STD_ID_LEN, BR250K, PORTB_8_9_WIRE_PULLUP); // 11b IDs, 250k bit rate, no transceiver chip, portA pins 11,12
  can.filterMask16Init(0, 0, 0x7ff, 0, 0);                // filter bank 0, filter 0: don't pass any, flt 1: pass all msgs
  pinMode(bluePillLED, OUTPUT);

  can.filterList16Init(2, RXPDO0_ID, RXSDO_ID, 0x71, 0x72);  // rx bank 2. passes IDs == 5, 10, 0x71 and 0x72

  can.attachInterrupt(canISR);
  // can.filterMask16Init(0, rxMsgID, 0x7ff);   // filter bank 0, filter 0: allow ID = rxMsgID, mask = 0x7ff (must match)
                                                // without calling a filter, the default passes all IDs
}

void measure (void){
  txpdo.vBatteryMillivolts = analogRead(PIN_vBattery);
  txpdo.iBatteryMilliamps  = analogRead(PIN_iBattery);
  txpdo.vChargerMillivolts = analogRead(PIN_vCharger);

  txpdo.flag.chargerConnected =
        (txpdo.vChargerMillivolts >= sdo.vChargerMin)
    &&  (txpdo.vChargerMillivolts <= sdo.vChargerMax);

  if (txpdo.vBatteryMillivolts < sdo.vBatteryMin){
    emergency(EMCY_BATTERY_DEAD);
  }
  else if (txpdo.vChargerMillivolts > sdo.vChargerMax){
    emergency(EMCY_CHARGER_OVERVOLTAGE);
  }

  else if (!txpdo.flag.charging){
    if (    (txpdo.flag.chargerConnected)
        &&  (txpdo.vBatteryMillivolts <= sdo.vBatteryStartCharge)
        &&  (txpdo.vBatteryMillivolts >= sdo.vBatteryMin)
    ){
      txpdo.flag.charging = 1;
      digitalWrite(PIN_CHARGER_ENABLE, HIGH);
      }
  }
  else{
  // charging is active
    if (txpdo.vBatteryMillivolts >= sdo.vBatteryMax){
      // battery is full, terminate charge
      txpdo.flag.charging = 0;
      digitalWrite(PIN_CHARGER_ENABLE, LOW);
    }
    else if (txpdo.vChargerMillivolts <= sdo.vChargerMin){
      // charger failed
      txpdo.flag.charging = 0;
      digitalWrite(PIN_CHARGER_ENABLE, LOW);
      emergency(EMCY_CHARGER_FAIL);
    }
  }


}


void loop() {
  uint32_t now;
  static uint32_t lastRun = 0;

  int id, fltIdx;


  now = millis();
  if (now - lastRun > MEASURE_LOOP_TIME){
    lastRun = now;
    measure();
  }

  // check for CAN received frames
  if (can.receive(id, fltIdx, CANrxBytes) > -1) // poll for rx
      digitalToggle(bluePillLED);

  //processRXPDO();
  //processSDO();
  //processMISC();

}

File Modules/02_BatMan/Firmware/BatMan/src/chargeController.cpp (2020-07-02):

/* charge Control
*
*/

#include <Arduino.h>
#include "chargeController.h"

/**
  Constructor
**/
chargeController::chargeController(
  uint8_t pwmPin,
  uint8_t pwmInverted,
  uint8_t enPin,
  uint8_t enInverted
){
  _enPin = enPin;
  _pwmPin = pwmPin;
  _enInverted = enInverted;
  _pwmInverted = pwmInverted;

  // disable charger
  _setChargerPWM(0);
  if (_enPin != 0) pinMode(_enPin, OUTPUT);

  // switch PWM off
  digitalWrite(_pwmPin, 0^_pwmInverted);
  pinMode(_pwmPin, OUTPUT);
}


void chargeController::_setChargerPWM(uint8_t n){
  if (n==0){
    if (_enPin != 0) digitalWrite(_enPin, 0^_enInverted);

    if (_pwmInverted)
      analogWrite(_pwmPin, 255);
    else
      analogWrite(_pwmPin, 0);
  }
  else{
    if (_pwmInverted) n = 255-n;
    if (_enPin != 0) digitalWrite(_enPin, 1^_enInverted);
    analogWrite(_pwmPin, n);
  }
}

/**
  \return current PWM value (mostly for testing)
**/
uint8_t chargeController::getPWM(void){
  return _pwmValue;
}

/**
  \brief Set callback function to measure battery voltage.

  Function should return battery voltage in millivolts
**/
void chargeController::setBatteryVoltageCB( uint16_t (*f)(void)  ){
  _batteryVoltageCB = f;
}

/**
  \brief Set callback function to measure battery voltage.

  Function should return battery voltage in millivolts
**/
void chargeController::setChargerVoltageCB( uint16_t (*f)(void)  ){
  _chargerVoltageCB = f;
}

/**
  \brief Set callback function to measure battery current.

  Function should return battery current in milliamps
**/
void chargeController::setBatteryCurrentCB( uint16_t (*f)(void)  ){
  _batteryCurrentCB = f;
}

/**
  \brief Set callback function to measure battery temperature.

  Function should return battery temperature in celsius
**/
void chargeController::setBatteryTemperatureCB( int8_t (*f)(void)  ){
  _batteryTemperatureCB = f;
}


uint8_t chargeController::charge(uint16_t iBattery, uint16_t vCharger){
static uint16_t charging = 0;

  // get momentary values
 _vBattery = _batteryVoltageCB();
 _vCharger = _chargerVoltageCB();

  if (vCharger < _vTerminateCharge+3000){
    _setChargerPWM(0);
    return CH_NO_CHARGER;
  }

  if (_vBattery < _vBatteryDead){
    _setChargerPWM(0);
    return CH_BATTERY_DEAD;
  }


  if (charging){
    // terminate charge
    if (    (_vBattery > _vTerminateCharge)
        ||  (_batteryTemperatureCB() > _tBatteryMax)
    ){
      charging = 0;
    }
    else{
      // continue charging
      // check voltage and current
      while (   (_batteryVoltageCB() <= _vTerminateCharge)
             && (_batteryCurrentCB() < _iChargeMax)
             && (_pwmValue < 255)
      ) _setChargerPWM(++(_pwmValue));

      while ( (  (_batteryVoltageCB() > _vTerminateCharge)
              || (_batteryCurrentCB() > _iChargeMax)
            ) && (_pwmValue > 0)
      ) _setChargerPWM(--(_pwmValue));
    }
    return CH_CHARGING;
  }
  else {
    // not (yet) charging
    _setChargerPWM(0);
    if (_vBattery <= _vBeginCharge){
      charging = 1;
    }
    return CH_DISCHARGING;
  }

  return 0;
}

void chargeController::setVoltageDead(uint16_t millivolt){
  _vBatteryDead = millivolt;
}
void chargeController::setVoltageBeginCharge(uint16_t millivolt){
  _vBeginCharge = millivolt;
}
void chargeController::setVoltageTerminateCharge(uint16_t millivolt){
  _vTerminateCharge = millivolt;
}
void chargeController::setChargeCurrentMax(uint16_t milliamp){
  _iChargeMax = milliamp;
}
void chargeController::setTemperatureMax(int8_t celsius){
  _tBatteryMax = celsius;
}

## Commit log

2020-07-02 Add files via upload
    Module Body, Files for differential
    [DiffAssy.FCStd, boxLowerShell_x1.stl, boxLowerShell_x1_Rev02.stl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]
2020-07-02 reorganized folders
    [DiffAssy.FCStd, boxLowerShell_x1_Rev02.stl, boxUpperShell_x1.stl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]
2020-07-02 reorg folders
    [DiffAssy.FCStd, boxLowerShell_x1.stl, boxLowerShell_x1_Rev02.stl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]
2020-07-02 further imports
    [anlenkhebel.FCStd, anlenkhebel.stl, axis.FCStd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]
2020-07-05 added .gitignore file
    [differential.scad, test.scad]
2020-07-20 various changes
    [ABH_axisBearingHolder.FCStd, BOM.xlsx, Flexible_Coupling.scad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]
2020-08-11 united various directories
    [bearing6002.FCStd, driveGearWheel.3mf, driveGearWheel.scad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]
2020-08-15 collected files, part I
    [MG995Dummy.FCStd, MG996Dummy.FCStd, forkHolderAssy.FCStd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]
2020-08-15 collected files, part II
    [1110101_axisAssy.FCStd, 1210101_axisCarrierPlate.FCStd, 1210201_lagerschale_608.FCStd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]
2020-08-31 added axis bearing holder
    [1210201_lagerschale_608.FCStd, CUAB_CustomAngleBracket.FCStd, driveGearWheel.3mf]
2020-08-31 files collected
    [1110101_axisAssy.FCStd, 1210101_axisCarrierPlate.FCStd, 1210201_lagerschale_608.FCStd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]
2020-09-09 daily update
    [1220403_axisHolderLeftOuter.stl, CUAB_CustomAngleBracket.FCStd]
